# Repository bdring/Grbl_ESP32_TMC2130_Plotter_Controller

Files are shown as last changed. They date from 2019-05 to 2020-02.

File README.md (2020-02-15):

## TMC2130 Pen / Laser Controller

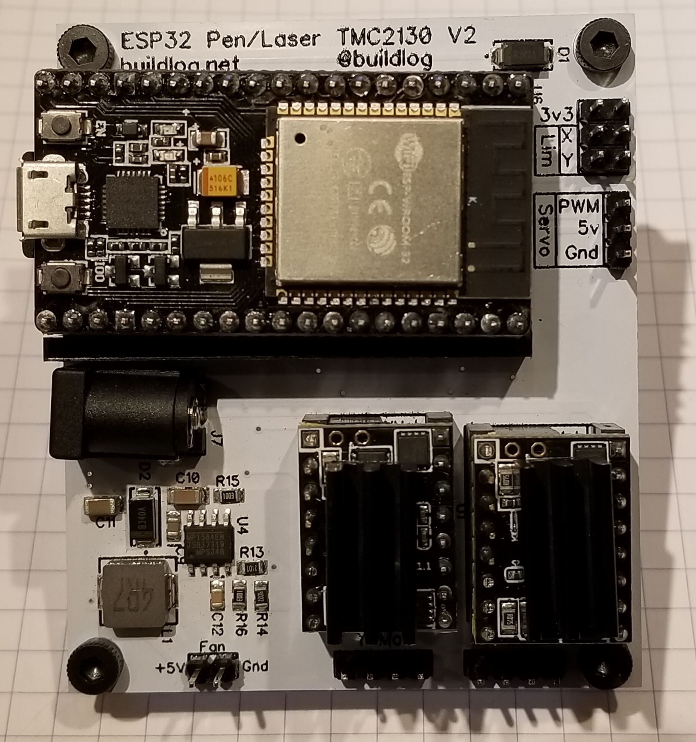
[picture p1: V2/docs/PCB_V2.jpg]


This is a simple controller for a Pen Plotter that uses Grbl_ESP32 as the firmware and TMC2130 stepper motor drivers in SPI mode. There is a hobby servo connector for pen up/down control. The PWM signal (3.3V TTL) on that could also be used to control a laser module.

### Features

- ESP32 Controller Socket
- SD Card Socket (under ESP32)
- (2) TMC2130 Stepper Driver Sockets (SPI Mode). Note: Non SPI drivers will not work.
- (2) Limit switch connectors
- Hobby Servo connector
- Strong 5V 3A power supply
- All the freaking awesome features of Grbl_ESP32

### Firmware

The firmware used is Grbl_ESP32. There is a special branch that supports the TMC2130.

### Open Source

- [Schematic](https://github.com/bdring/Grbl_ESP32_TMC2130_Plotter_Controller/blob/master/V2/docs/schematic_v2.pdf)
- [Gerber Files](https://github.com/bdring/Grbl_ESP32_TMC2130_Plotter_Controller/tree/master/gerbers)
- [BOM](https://github.com/bdring/Grbl_ESP32_TMC2130_Plotter_Controller/blob/master/docs/BOM.csv)
- [Source files (DipTrace)](https://github.com/bdring/Grbl_ESP32_TMC2130_Plotter_Controller/tree/master/source)

### Version History

- V2
   - Moved X Limit Switch form GPIO 2 to 32. Works better on dev boards that have an LED on that pin.
   - The footprint for the stepper drivers no include the diag pins
   - Added jumpers to optional connect diag pins to limit pins
   - Grounded TMC2130 N/C pin to make it compatible with TMC5160 drivers. The capacitor size is probably not ideal for use with the full capacity of the TMC5160, but should work.
   - Added 5V output (fan connector)

### Getting Started

- [Wiki for this design](https://github.com/bdring/Grbl_ESP32_TMC2130_Plotter_Controller/wiki)
- [Wiki for Grbl_ESP32](https://github.com/bdring/Grbl_Esp32/wiki)
- Getting one. I have a few extra, just ask for one via [this Issue.](https://github.com/bdring/Grbl_ESP32_TMC2130_Plotter_Controller/issues/1)

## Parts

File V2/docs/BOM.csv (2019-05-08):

RefDes | Description | Value | Manufacturer | Mfg P/N | Link | Price | Qty
C1,C5 | Capacitor, Electrolytic | 47u 35V | Nichicon | UWX1V470MCL1GB | https://www.digikey.com/short/p80qq5 | 0.15 | 5
C7,C8,C9 | Capacitor, Ceramic | 100nF 50V | Kemet | C0805C104K5RACAUTO | https://lcsc.com/product-detail/Multilayer-Ceramic-Capacitors-MLCC-SMD-SMT_KEMET_C0805C104K5RACAUTO_100nF-104-10-50V-Car-level_C129641.html | 0.011 | 8
C10 | Capacitor, Ceramic | 10uF | Taiyo Yuden | GMK316BJ106KL-T | https://lcsc.com/product-detail/Multilayer-Ceramic-Capacitors-MLCC-SMD-SMT_Taiyo-Yuden-GMK316BJ106KL-T_C92797.html | 0.07 | 1
C11 | Capacitor, Ceramic | 22uF 6.3V | Taiyo Yuden | JMK316BJ226KL-T | https://lcsc.com/product-detail/Multilayer-Ceramic-Capacitors-MLCC-SMD-SMT_TAIYO-YUDEN_JMK316BJ226KL-T_22uF-226-10-6-3V_C92791.html | 0.07 | 1
C12 | Capacitor, Ceramic | 150pF 50v 0805 | CCTC | TCC0805X7R151K500BT | https://lcsc.com/product-detail/Multilayer-Ceramic-Capacitors-MLCC-SMD-SMT_CCTC-TCC0805X7R151K500BT_C282743.html | 0.01 | 1
D1,D2 | Diode, Schottkey | diode, Schottkey 3A | (MDD) Jiangsu Yutai Elec | (MDD) Jiangsu Yutai Elec | https://lcsc.com/product-detail/Schottky-Barrier-Diodes-SBD_Jiangsu-Yutai-Elec-B340A_C64982.html | 0.22 | 3
U6,J1 | Connector, Header | ESP-32 Header Female 1x19 0.1" |  |  | https://www.aliexpress.com/item/100Pcs-Per-Lot-2-54mm-Pitch-1x19-Pin-19-Pin-Female-Single-Row-Straight-Header-Strip/32760221364.html | 0.35 | 3
J2,J4 | Connector, Header | Header Male 1x4 0.1" | TE Connectivity |  | https://lcsc.com/product-detail/Male-Header_2-54mm-1-4P-HeaderG-FRegular_C152150.html | 0.017 | 2
J3 | Connector, Header | Header 1x6
J5 | Connector, Header | Header 1x3
J7 | Connector, Barrel
J8 | Socket, Micro SD | Micro SD Socket | Korean Hroparts Elec TF-01A | TF-01A | https://lcsc.com/product-detail/Connector-Card-Sockets_Korean-Hroparts-Elec-TF-01A_C91145.html | 0.13 | 1
L1 | Inductor | Inductor 4.7uH 5.5A | Chilisin Elec | MHCI06030-4R7M-R8 | https://lcsc.com/product-detail/Power-Inductors_Chilisin-Elec-MHCI06030-4R7M-R8_C108295.html | 0.0875 | 1
R9,R10 | Inductor | Inductor 4.7uH 5.5A | Chilisin Elec | MHCI06030-4R7M-R8 | https://lcsc.com/product-detail/Power-Inductors_Chilisin-Elec-MHCI06030-4R7M-R8_C108295.html | 0.0875 | 1
R13 | Resistor | 210k | YAGEO | AC0805FR-07210KL | https://lcsc.com/product-detail/Others_YAGEO-AC0805FR-07210KL_C228629.html | 0.003 | 1
R14 | Resistor | 40.2k | YAGEO | AC0805FR-0740K2L | https://lcsc.com/product-detail/Others_YAGEO-AC0805FR-0740K2L_C228820.html | 0.004 | 1
R15,R16 | Resistor | 100k | YAGEO | AC0805FR-07100KL | https://lcsc.com/product-detail/Chip-Resistor-Surface-Mount_100KR-1003-1_C144587.html | 0.003 | 2
U2,U3 | Connector, Header | Header Female 1x8 0.1" |  |  | https://lcsc.com/product-detail/Female-Header_2-54mm-1-8P-Straight-Female-header_C27438.html | 0.05 | 4
U4 | DC-DC Power Supply Controller | MP1584EN | Monolithic Power Systems | MP1584EN-LF-Z | https://lcsc.com/product-detail/DC-DC-Converters_MPS_MP1584EN-LF-Z_MP1584EN-LF-Z_C15051.html | 0.28 | 1

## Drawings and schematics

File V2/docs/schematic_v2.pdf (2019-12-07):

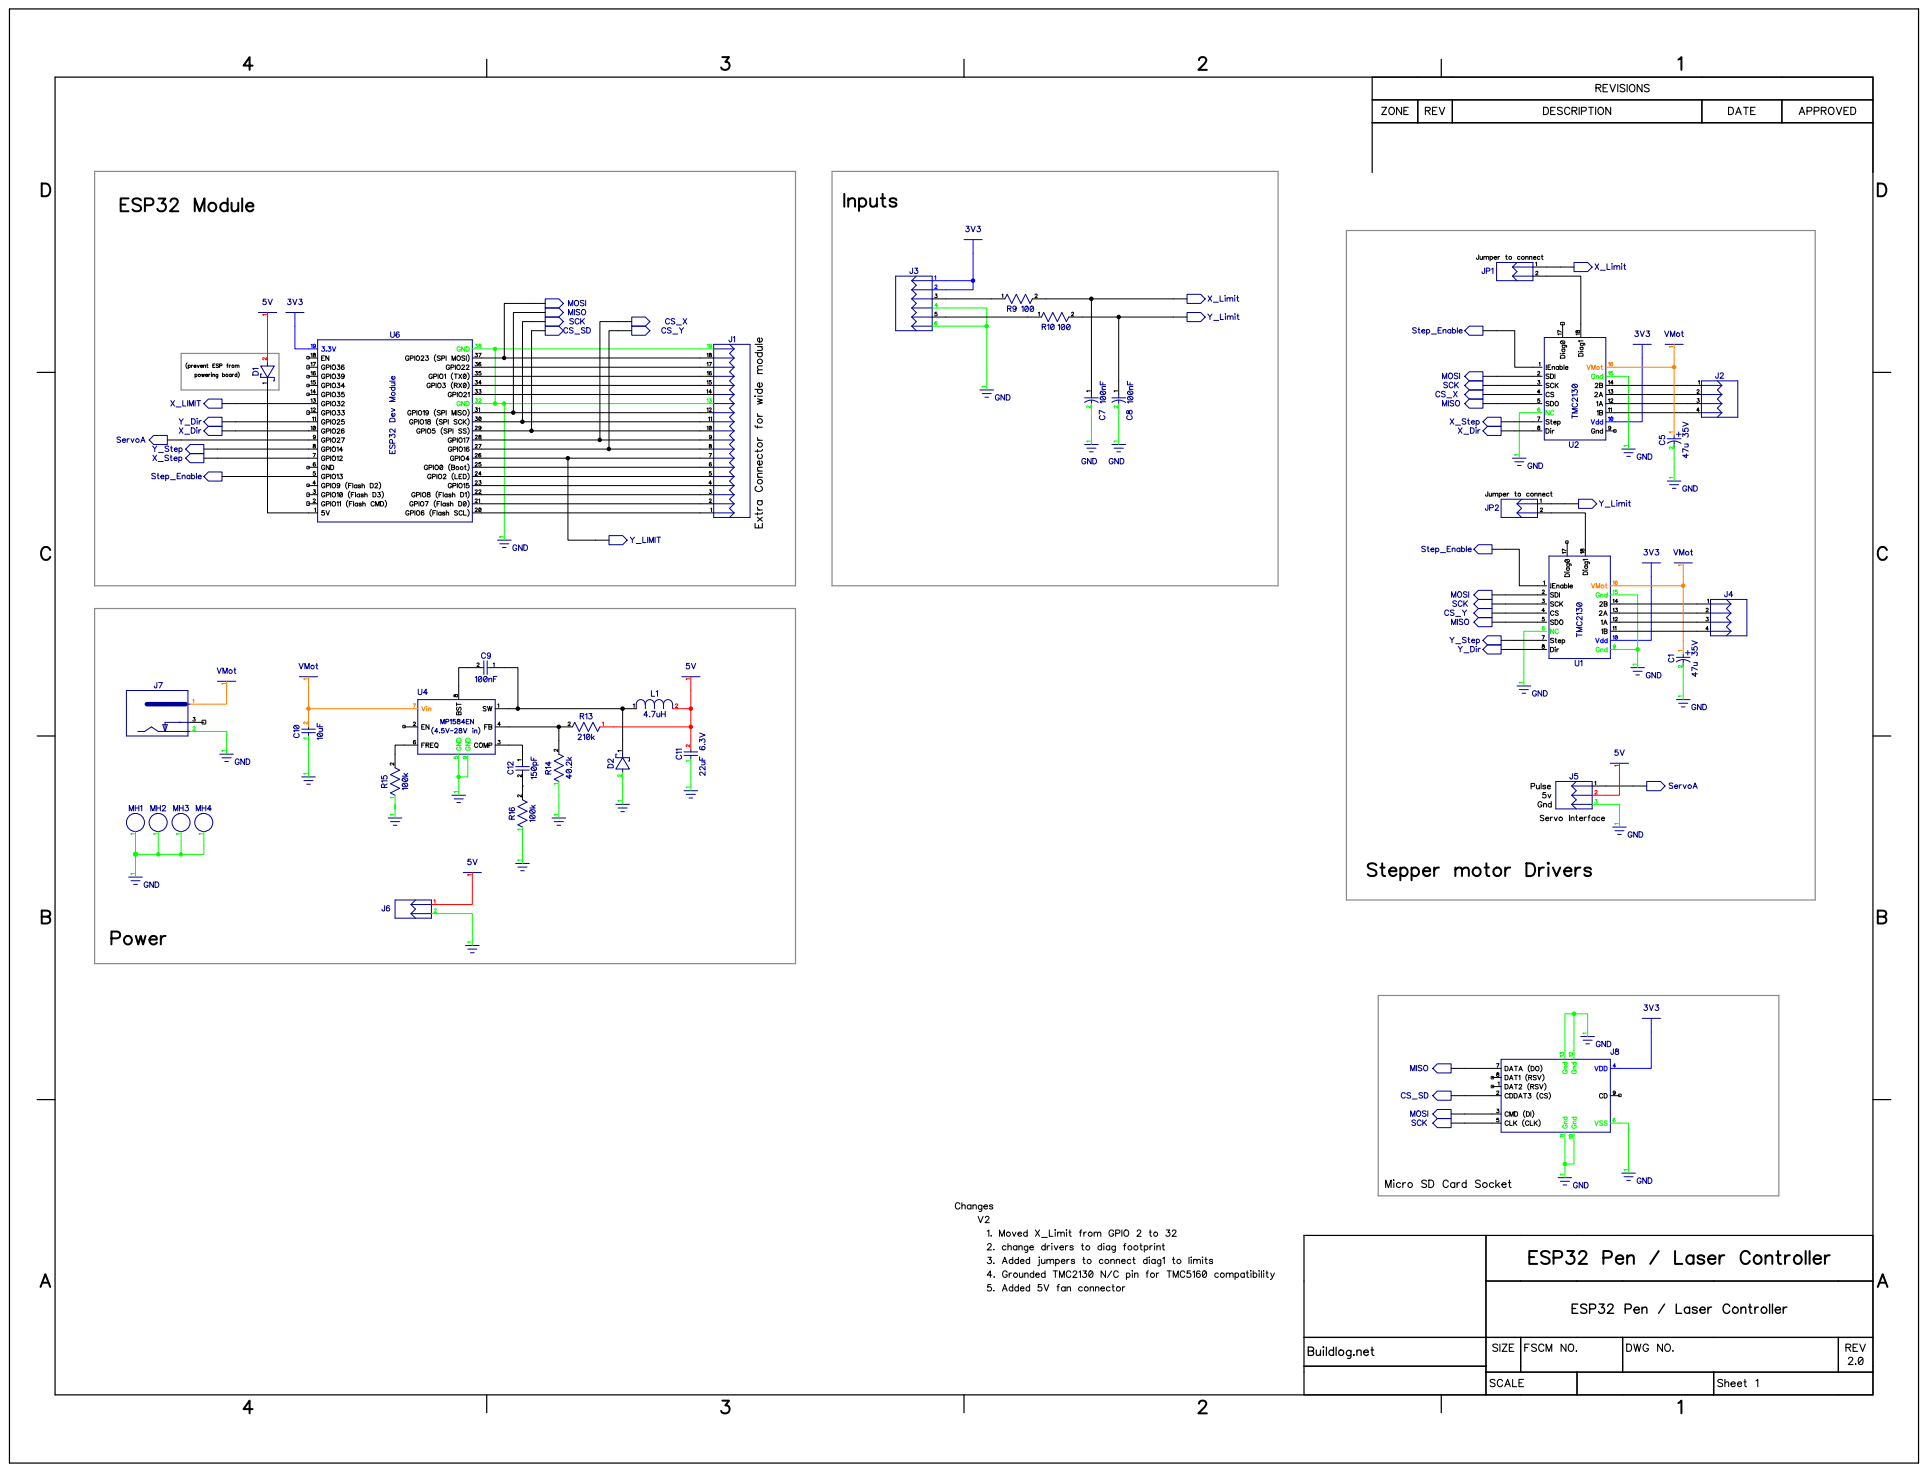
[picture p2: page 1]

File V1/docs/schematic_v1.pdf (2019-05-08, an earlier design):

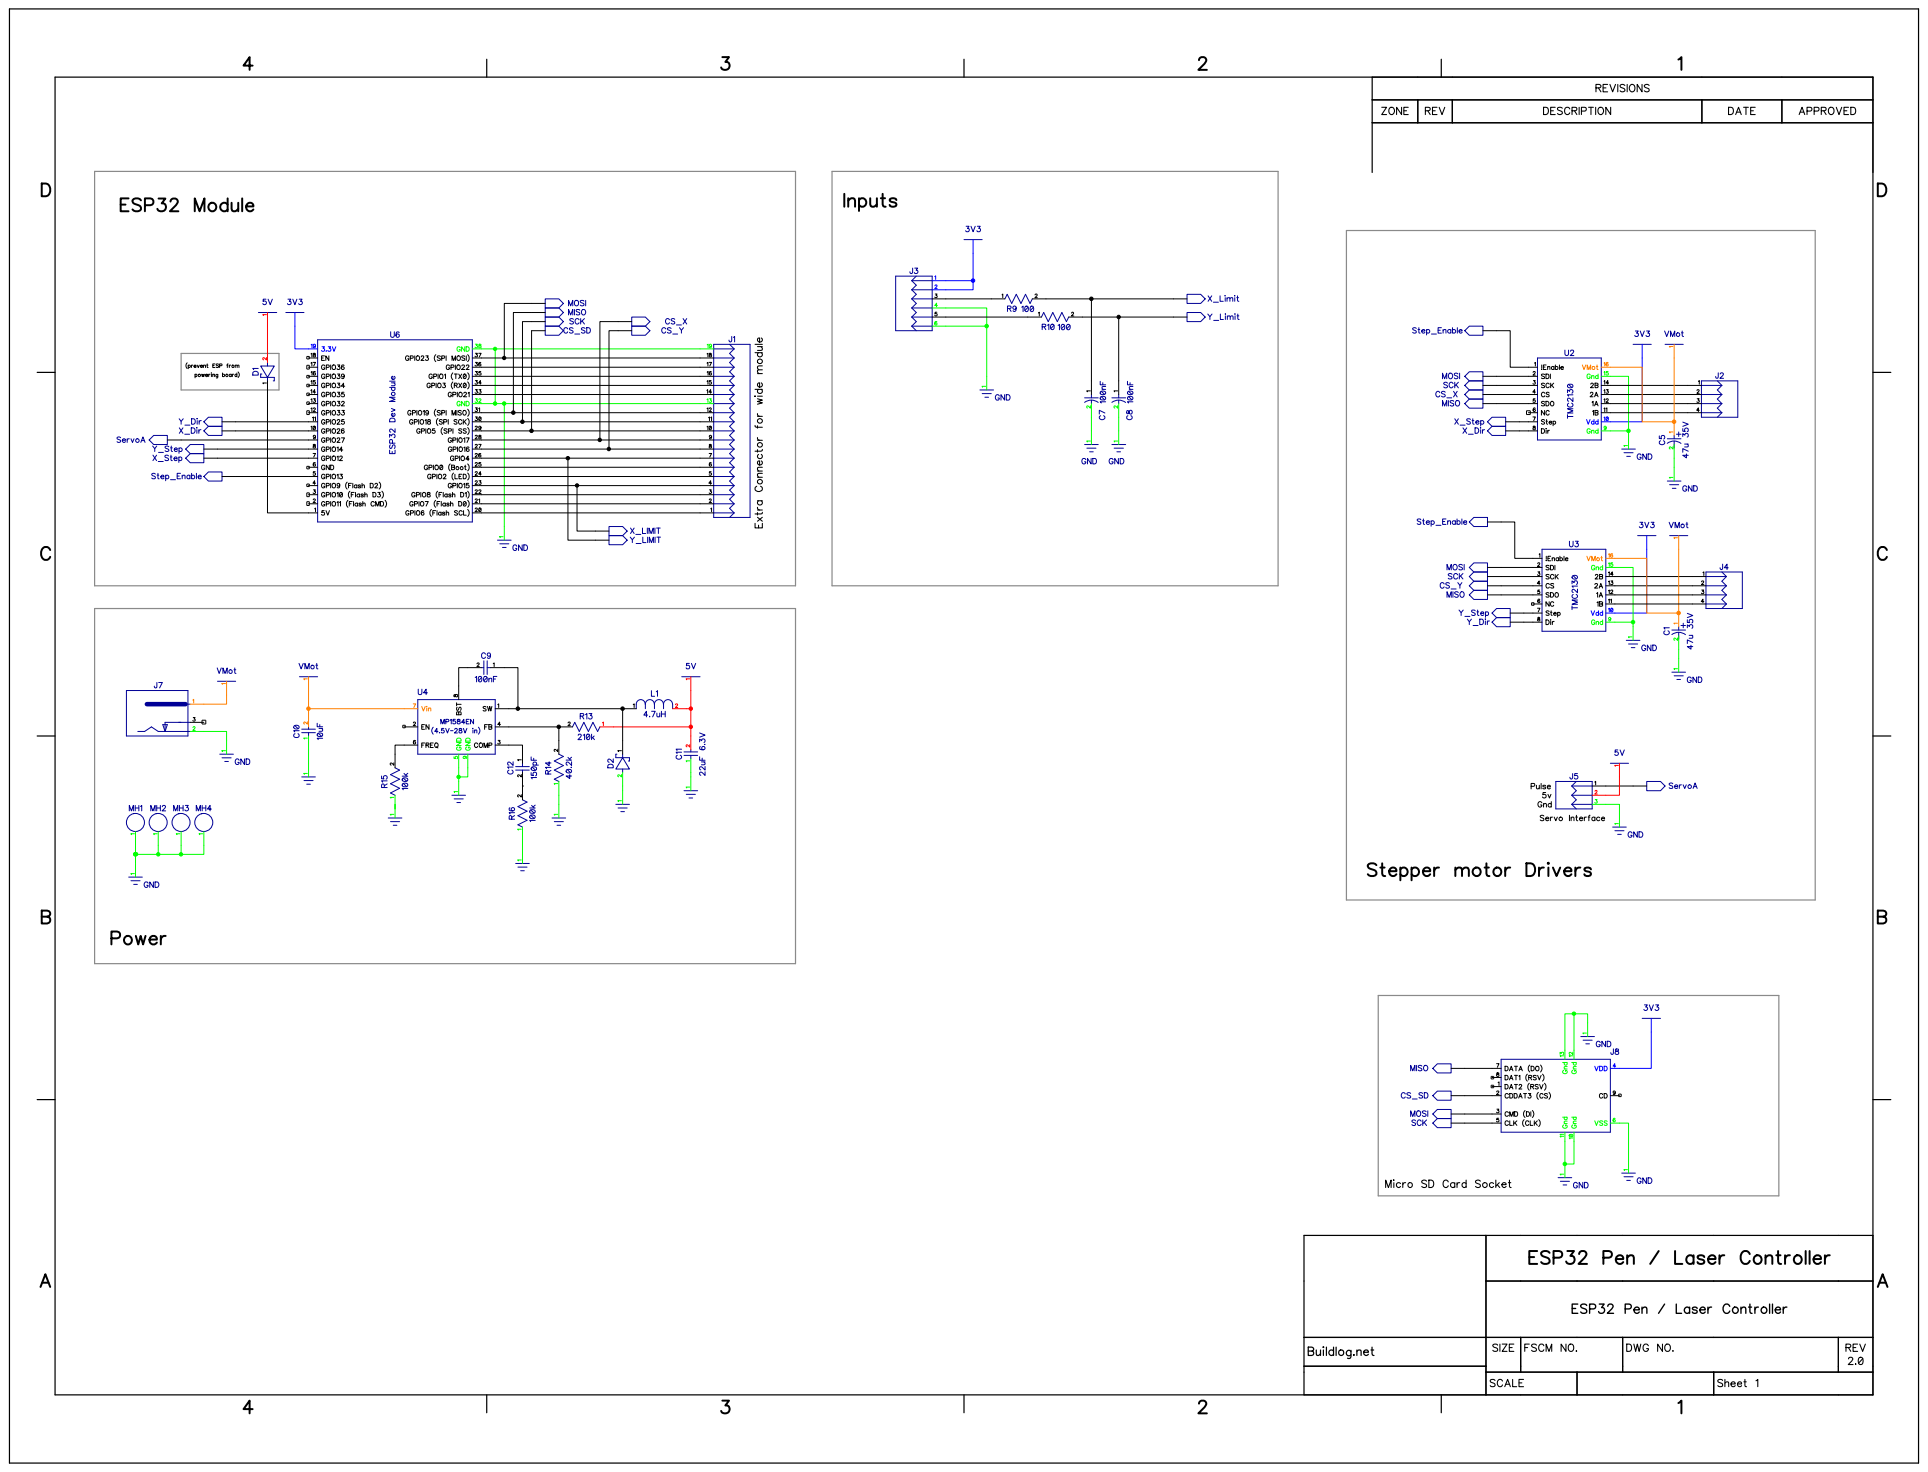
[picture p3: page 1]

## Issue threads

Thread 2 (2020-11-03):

TMC2130

dementiev-net, 2020-11-03:
Hi.
Great project!
And which UART driver will work exactly with this board? TMC2130 is very hard to find. Thanks!

bdring, 2020-11-04:
We do not support Trinamic Motors with UART in Grbl_ESP32 and that board is probably not wired for it anyway. You must use TMC2130 drivers in SPI mode.

They are very easy to get for most people. Amazon, eBay, AliExpress.

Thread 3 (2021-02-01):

Servo control for the pen

maximius, 2021-02-01:
Good afternoon, Bart.
Thank you very much for your work. I want to build a Drawing Robot (CoreXY mechanics), based on your controller. But there was one question about working with servo.

I use the GRBL v1.3a firmware. Configuration of pen_laser. h. I configured the laser control successfully(on the PWM pin with a frequency of 5 kHz, the duty cycle changes when the parameter S changes within 0-255)

When I select #define USE_PEN_SERVO in config.h. in the configuration, the pulse frequency on the PWM pin becomes 50 Hz (pulse length 2ms), but when changing the position of the servo (for example, m3 s10 or m3 s20), the pulse length does not change. and the pulses start to be generated only when the axes are moved. I tried different configurations and settings, but I didn't learn how to change the position of the servo.
I ask for help in this matter. How to properly control the servo to move the handle?
While using RBL_Servo on the arduino Uno and to control the servo, the commands m3 s3 for moving down and m5 for lifting the handle are used.
